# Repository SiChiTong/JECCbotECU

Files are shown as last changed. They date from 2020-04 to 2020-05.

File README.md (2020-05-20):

# JECCbotECU

See Istrobot 2020 demo video of JECCbot mini with JECCbotECU solving task of RoboOrienteering (https://robotika.vosrk.cz/roboorienteering/index.php?year=2020&page=aktuality ): https://www.youtube.com/watch?v=Fceis1Gl848 .

This Repository contains everything about controlling the JECCbot mini ( https://github.com/generationmake/JECCbot_mini ) with a the JECCbotECU board. There is also included software with web frontend for a Raspberry Pi, to move the robot to GPS waypoints.

## Hardware

### PCB

The JECCbotECU is formed from the controller board ( data included in this repository ) and some motor driver stage ( tested with https://github.com/generationmake/HighPowerMotorFeatherWing/ ). The controller pcb in this repository features a Bosch BNO055 IMU, the connection of a KVH C100 compass unit, GPS and RPLidar, USB VCOMM, different voltage regulators, GPIO port and SW-Debugging.

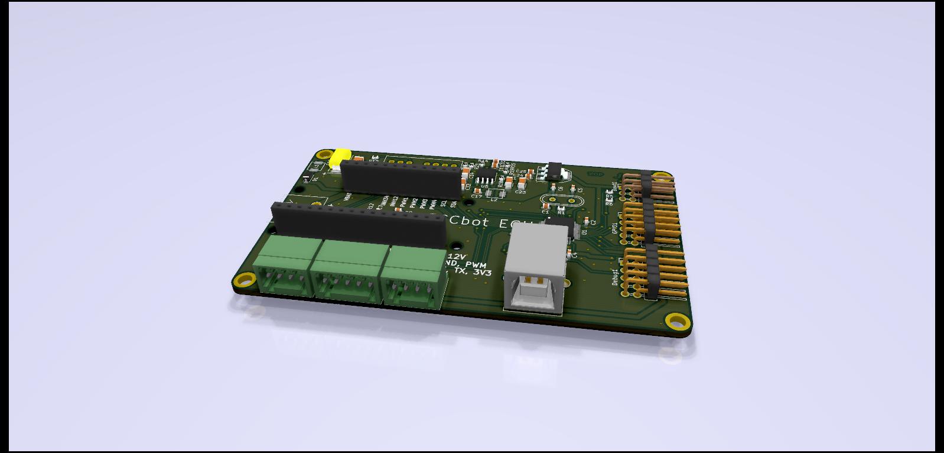
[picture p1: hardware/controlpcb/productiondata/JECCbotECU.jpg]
JECCbotECU rendering


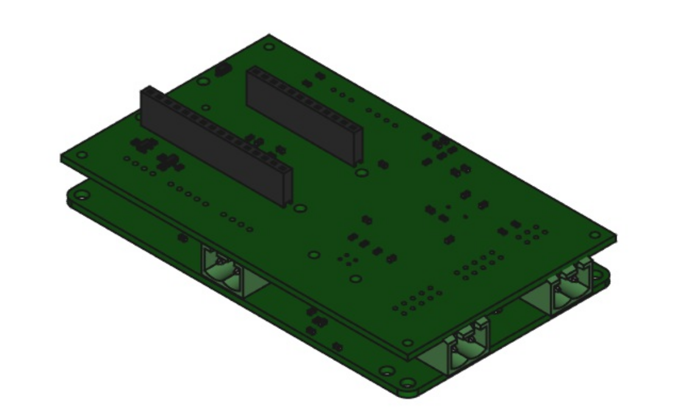
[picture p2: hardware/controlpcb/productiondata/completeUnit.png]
JECCbotECU with HighpowerMotorFeatherwing


### Case

There is also a case for the ECU unit with HighpowerMotorFeatherwing in this repository. It's size is 12cm x 10cm and it is fully compatible with the mountingholes on the JECCbot mini. On the top of the case, there is a snap in holder for a Einhell PowerXChange 18V drill battery.

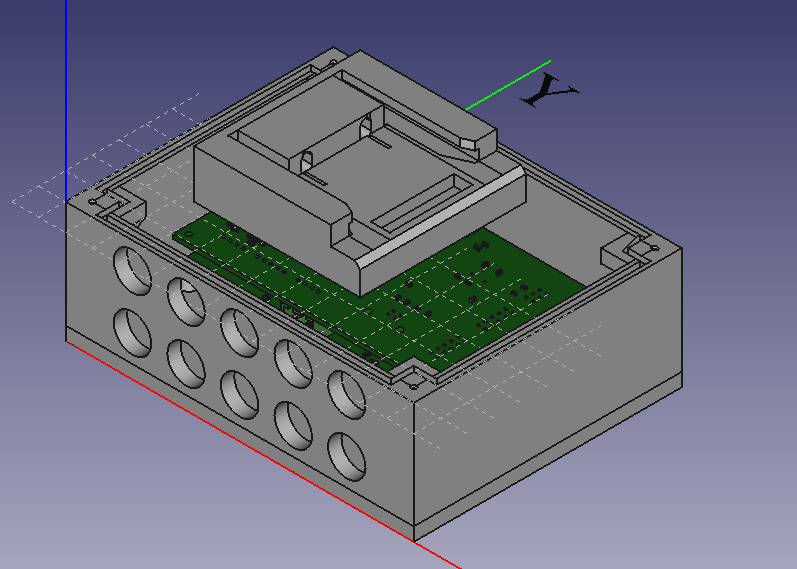
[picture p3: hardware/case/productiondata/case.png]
JECCbotECU case


## Software

### ECU 
 
The ECU Software is written in C using the STM32 Cube HAL hardware abstraction layer. It currently features control of two dc motors, emergency stop, rplidar, gps and compass decoding and driving the robot along a heading to north.

Here You can see the configured pinout of the STM32F103C8T6 mikrocontroller, which is compatible to STM32 Bluepill evalboard:

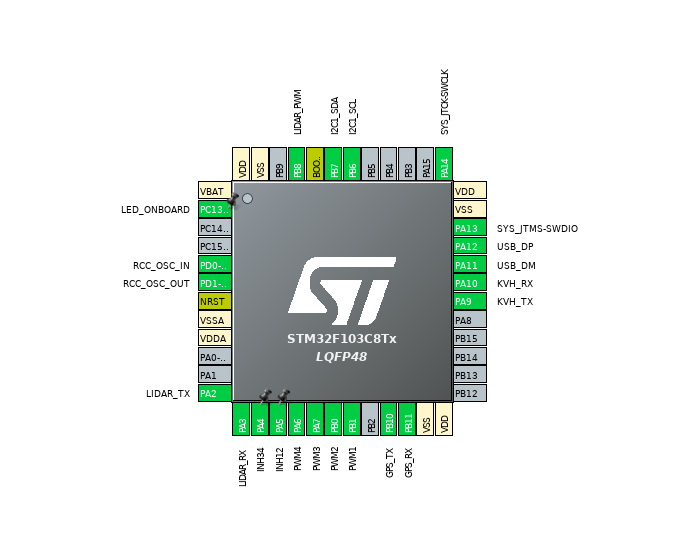
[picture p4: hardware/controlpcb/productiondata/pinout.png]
JECCbotECU pinout


#### Computer interaction

The ECU can interact with computer by using USB and a state based api.

##### Description of implemented states

###### State 0 - Joydrive

The direction and speed of the motors can be manipulated with the registers ```PWM_LEFT``` and ```PWM_RIGHT```. The value ranges are int16.

###### State 1 - Drive along compass heading

The robot can drive along a heading from -180° to 180° saved in the ```MOVEHEADING_HEADING``` register with a int16 speed in ```MOVEHEADING_SPEED``` by using a P-Controller with the parameter register ```MOVEHEADING_P```.

#### Protocol

The protocol is leaned on ASCII-Modbus and is register based. 

Every protocol instruction message begins with ```:```, which is followed with a 8 bit instructor. Then there is a 16 bit hex register address and a 16 bit or 32 bit hex register value ( interpreted as signed int ). Every message ends with ```\n```: 

```:<instructor><hex address><hex value>\n```

The mikrocontroller answers with ```:```, the register, value and ```\n```;

###### Protocol Configuration

```
API_MEMORY_SIZE 400

API_STATE_JOYDRIVE 0x0000
API_STATE_MOVEHEADING 0x0001

API_INSTRUCTION_READ 0x02
API_INSTRUCTION_WRITE 0x04

API_ERROR_WRONG_FORMAT 0x0000
API_ERROR_INVALID_ADDRESS 0x0001
API_ERROR_WRONG_INSTRUCTOR 0x0002
API_ERROR_ACCESS_DENIED 0x0003

API_REG_STATE 0x0000

API_REG_PWMLEFT 0x0002
API_REG_PWMRIGHT 0x0004

API_REG_MOVEHEADING_P 0x0005
API_REG_MOVEHEADING_SPEED 0x0006
API_REG_MOVEHEADING_HEADING 0x0007

API_BENCH_LIDAR_START 0x000f
API_BENCH_LIDAR_END API_BENCH_LIDAR_START + 360

API_REG_HEADING_KVH 0x0178

API_BENCH_GPS_START 0x0179
API_BENCH_GPS_END API_BENCH_GPS_START + 5
```

###### Example

Set robot state to 1:

Instruction: ```:04000000001\n``` -> Response ```:00000001\n```.

###### Error Codes

Every error code starts with the command e and has a specific index ( %03d ) as parameter, e. g. ```:e001\n```.

| Index | Meaning |
| ----- | ------- |
| 000 | received data is no command |
| 001 | Command is not found |
| 002 | Syntax error in command |

#### KVH Terminal

There is also a program included that lets the ECU act as a terminal to a connected KVH C100 compass unit. This can be used for calibrating the compass.

### Raspberry Pi

The main sotware used in the demonstration for Istrobot 2020 ( https://www.youtube.com/watch?v=Fceis1Gl848 ) is also included as a Codeblocks project.
In the html folder You can find the frontend design with commands to the robot via HTTP POST.

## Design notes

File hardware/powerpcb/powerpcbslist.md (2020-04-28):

# List of supported motor control / power pcbs

Generationmake HighpowermotorFeatherwing: https://github.com/generationmake/HighPowerMotorFeatherWing

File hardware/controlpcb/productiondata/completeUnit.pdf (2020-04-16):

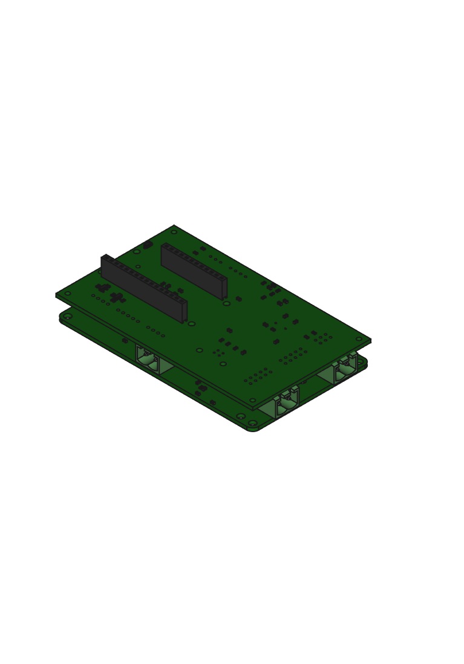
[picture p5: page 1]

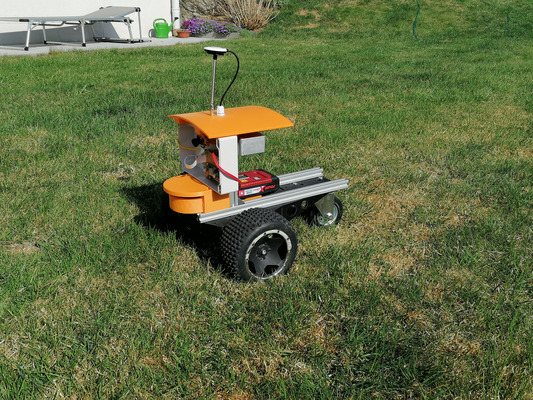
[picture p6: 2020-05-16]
software/html/titleImage.jpg

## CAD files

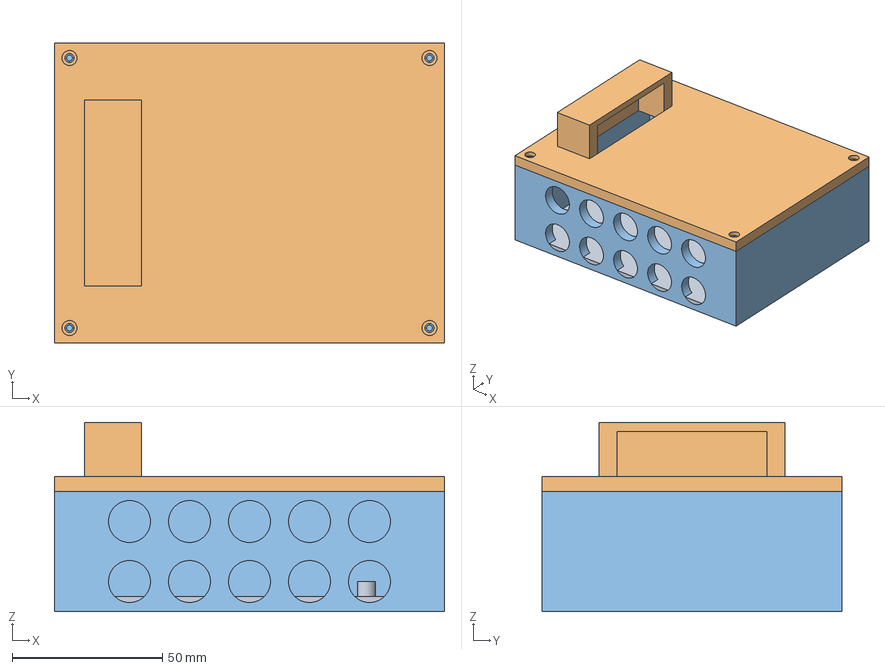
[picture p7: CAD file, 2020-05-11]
hardware/case/freecad/case.FCStd
130.0 x 100.0 x 63.0 mm
bottom
top
middle

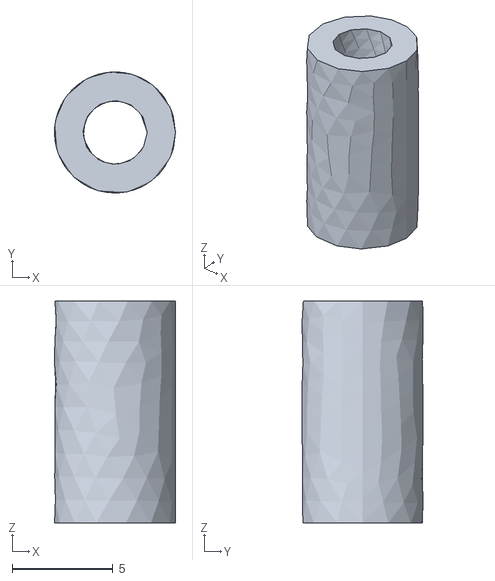
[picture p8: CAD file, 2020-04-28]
hardware/case/productiondata/spacer.stl
6.00 x 6.00 x 11.0

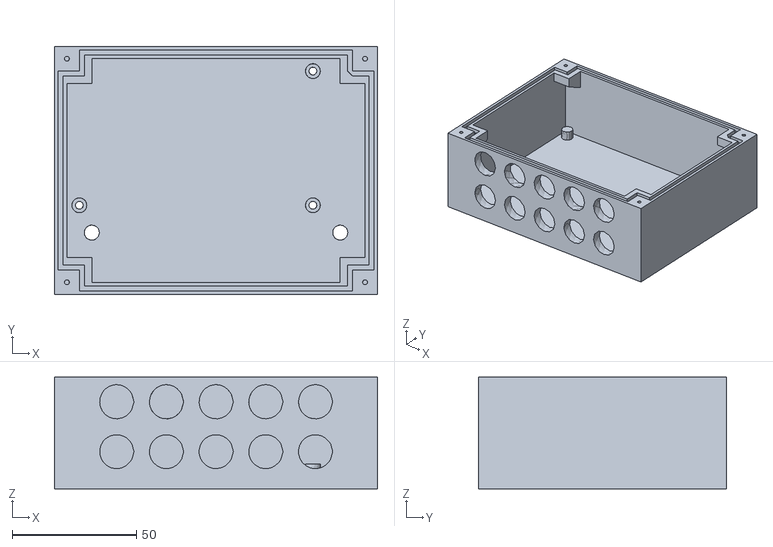
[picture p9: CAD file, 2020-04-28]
hardware/case/productiondata/lowercase.stl
130.0 x 100.0 x 45.0

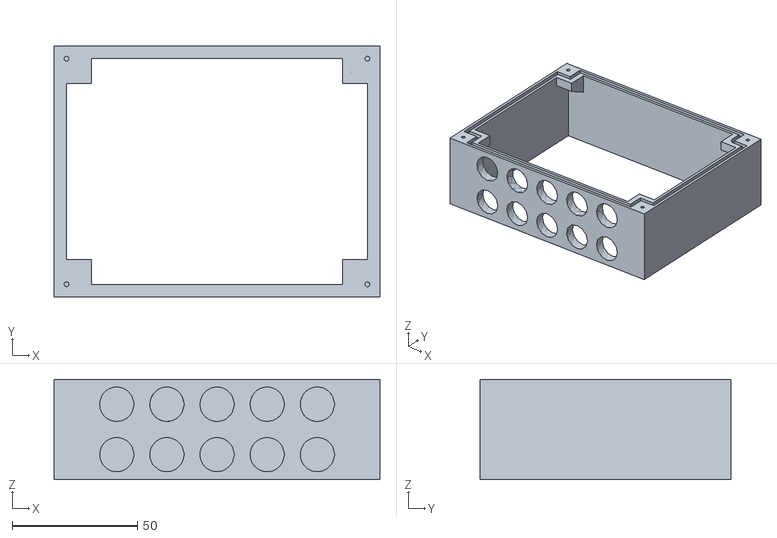
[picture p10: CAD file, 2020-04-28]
hardware/case/productiondata/middle.stl
130.0 x 100.0 x 40.0

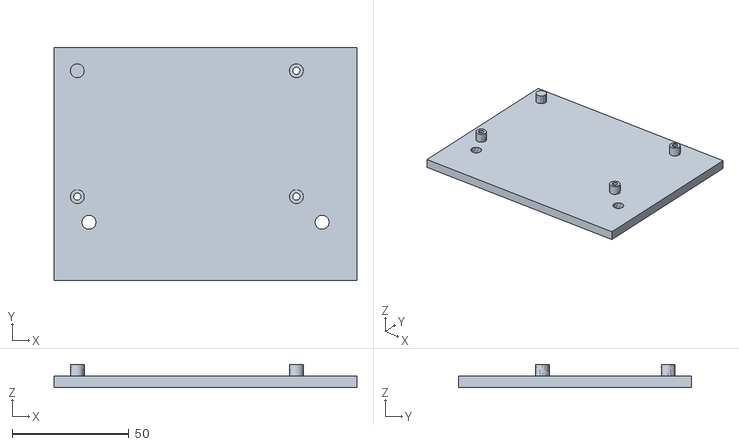
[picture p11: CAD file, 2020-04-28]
hardware/case/productiondata/bottom.stl
130.0 x 100.0 x 10.0

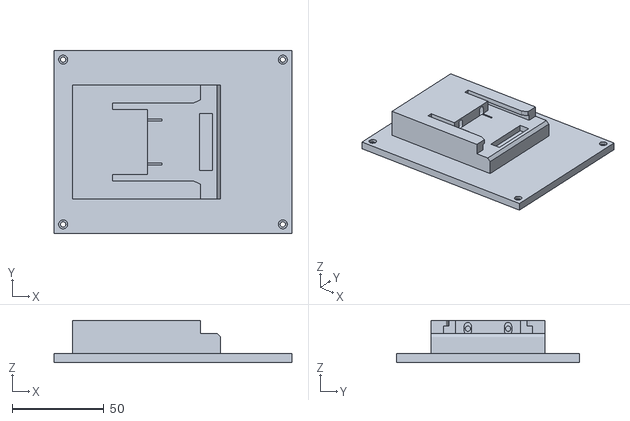
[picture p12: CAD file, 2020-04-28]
hardware/case/productiondata/uppercase.stl
130.0 x 100.0 x 23.0

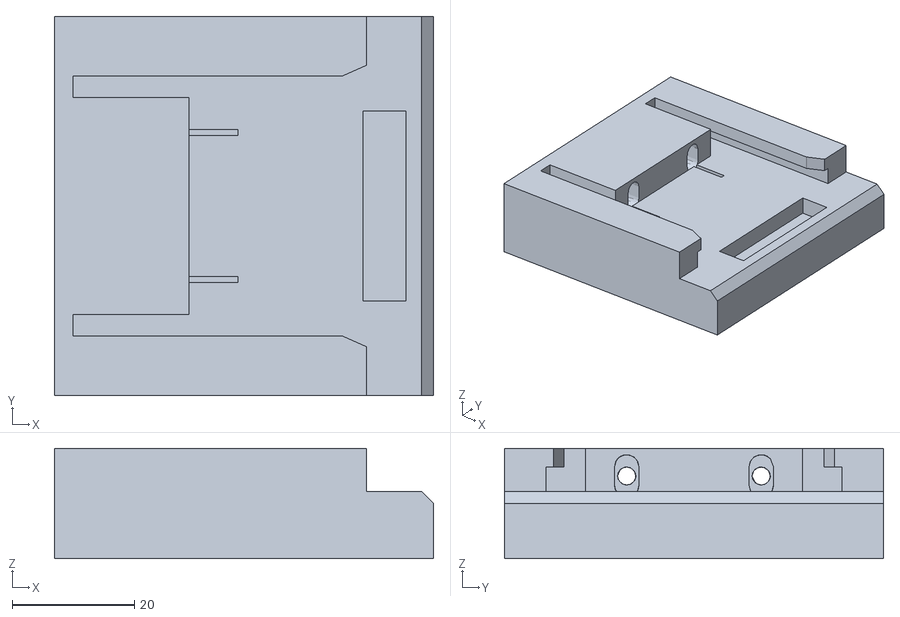
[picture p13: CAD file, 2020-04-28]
hardware/case/productiondata/batteryadapter.stl
62.0 x 62.0 x 18.0

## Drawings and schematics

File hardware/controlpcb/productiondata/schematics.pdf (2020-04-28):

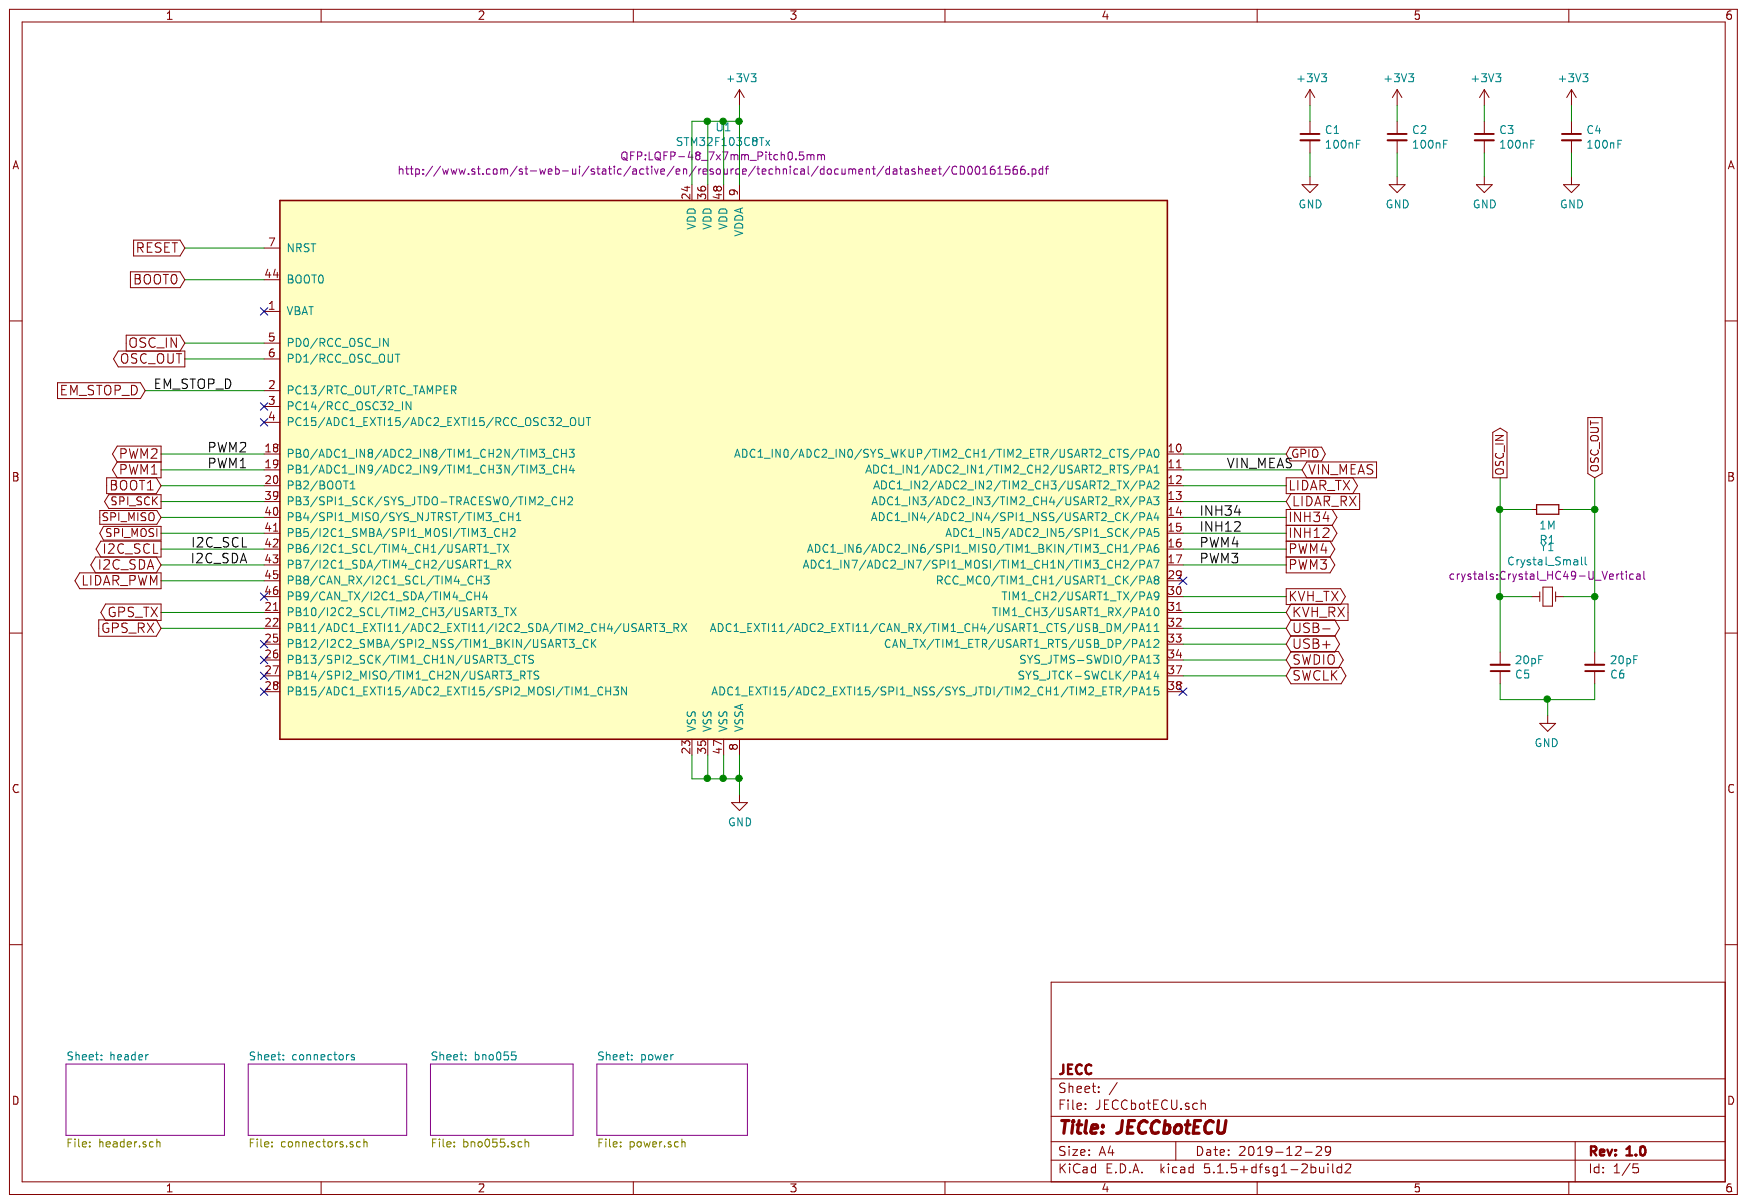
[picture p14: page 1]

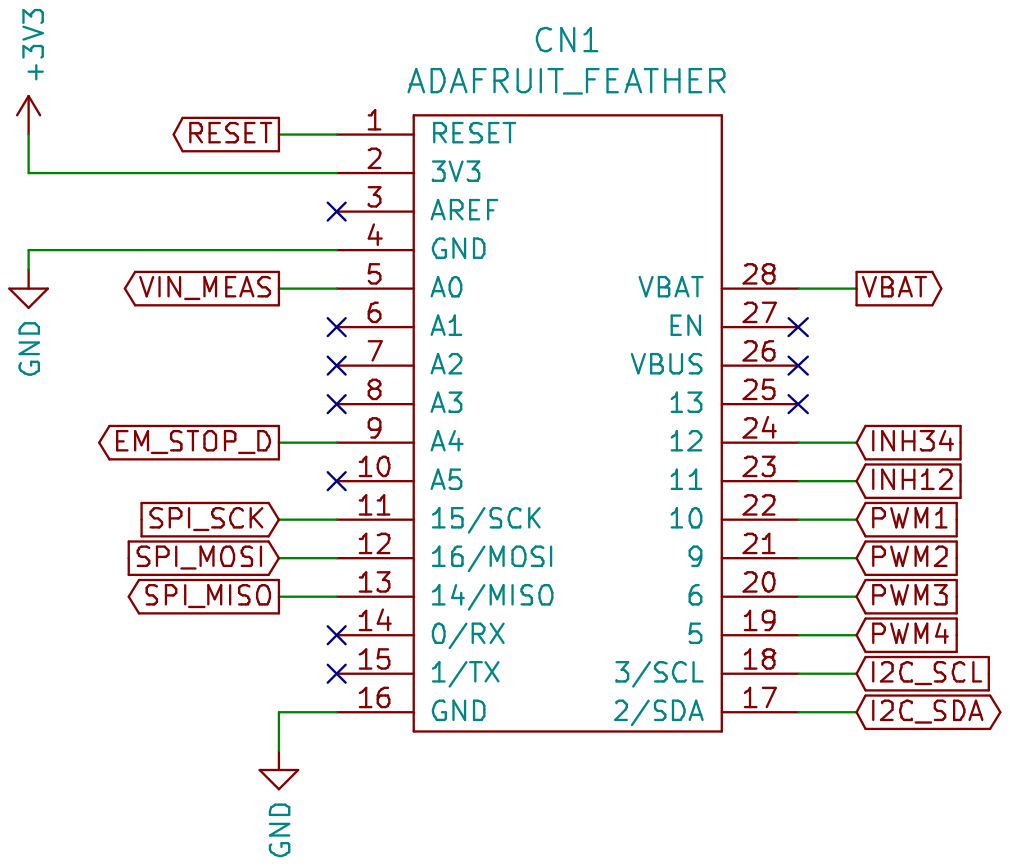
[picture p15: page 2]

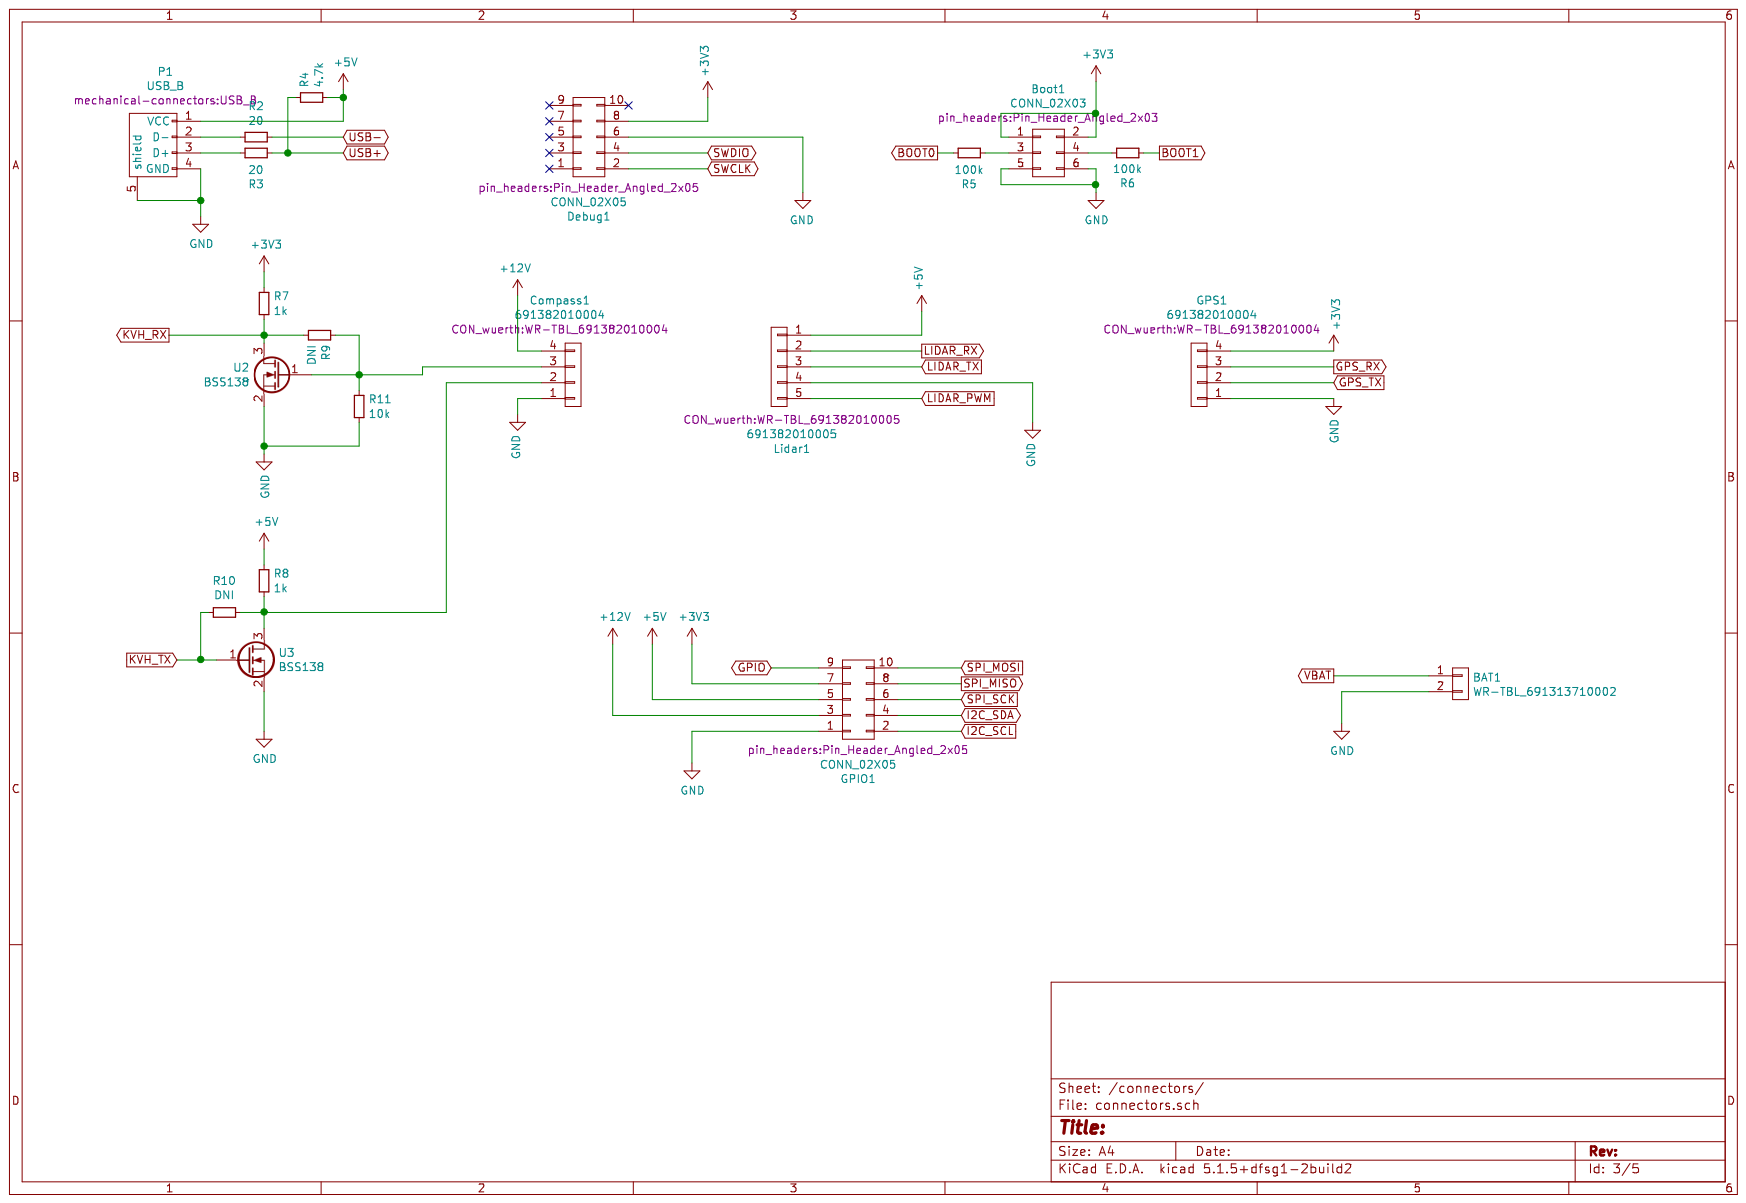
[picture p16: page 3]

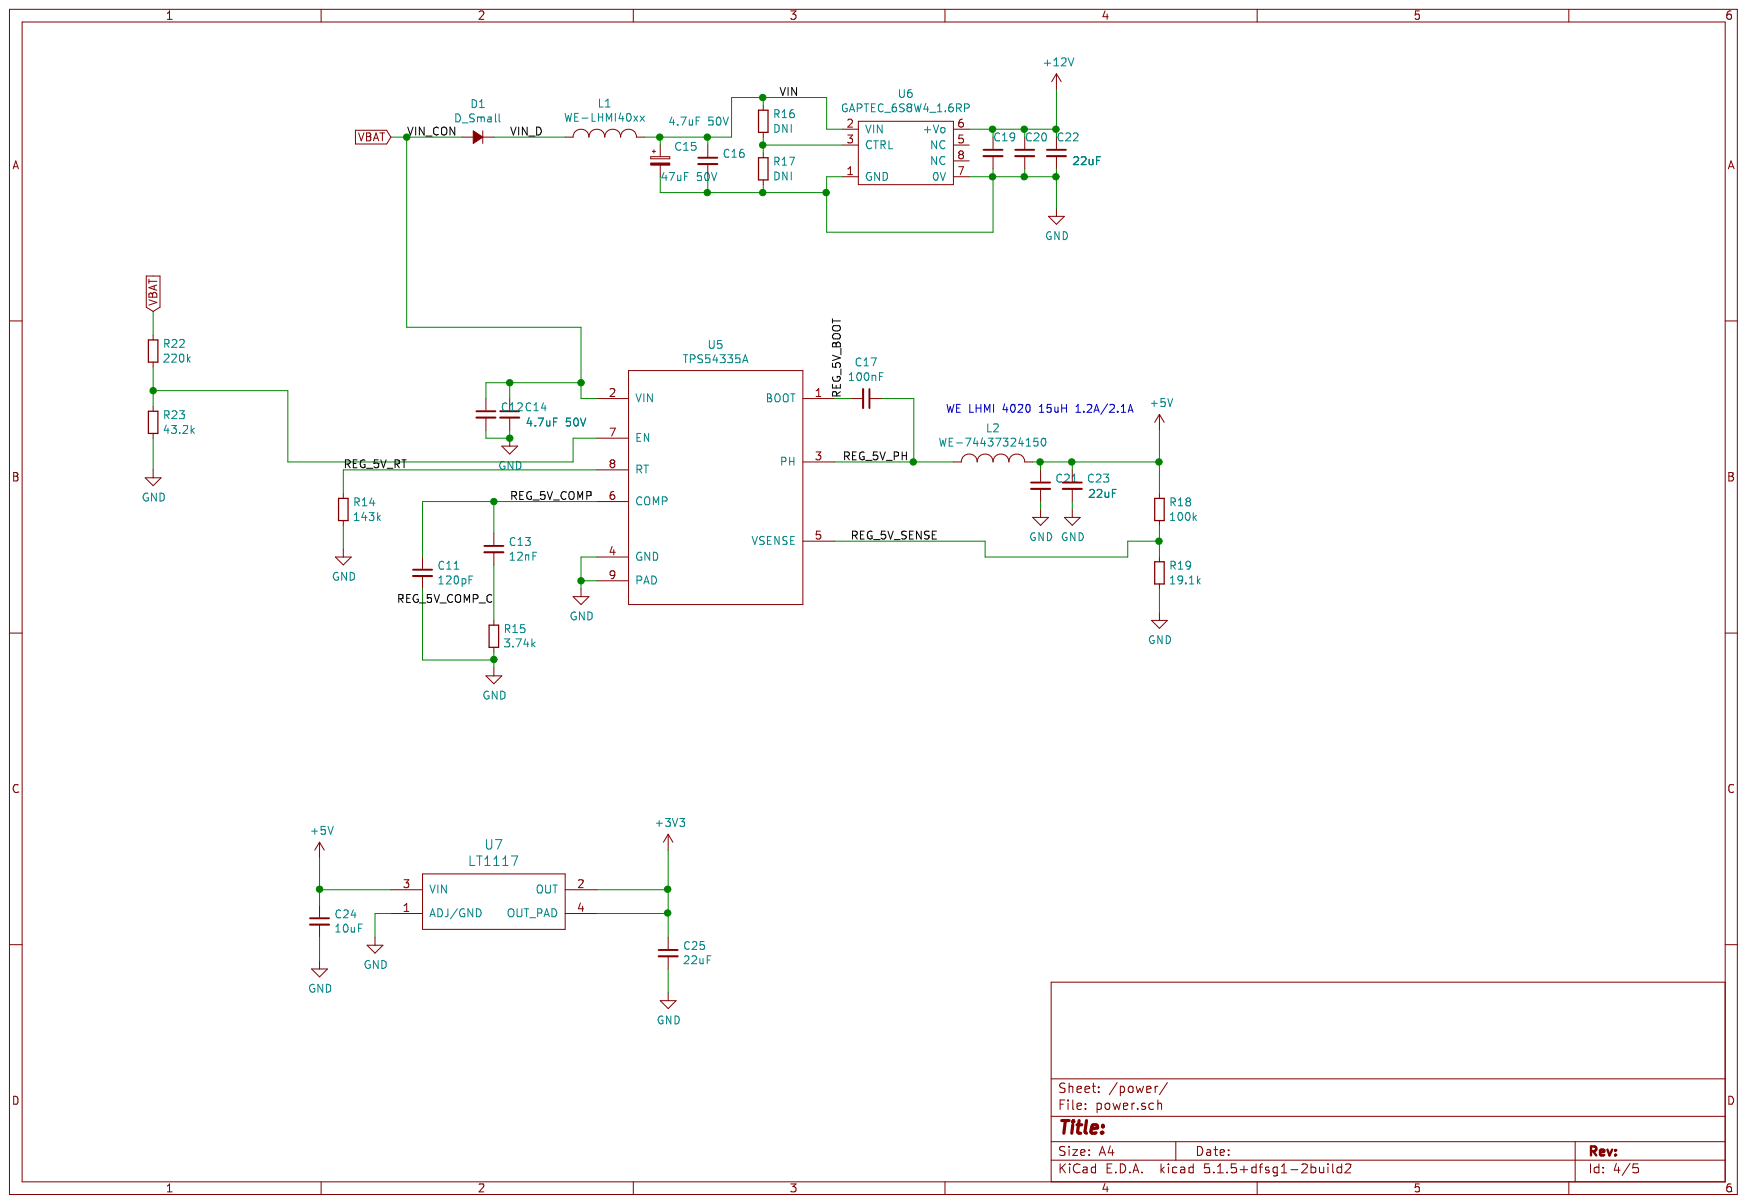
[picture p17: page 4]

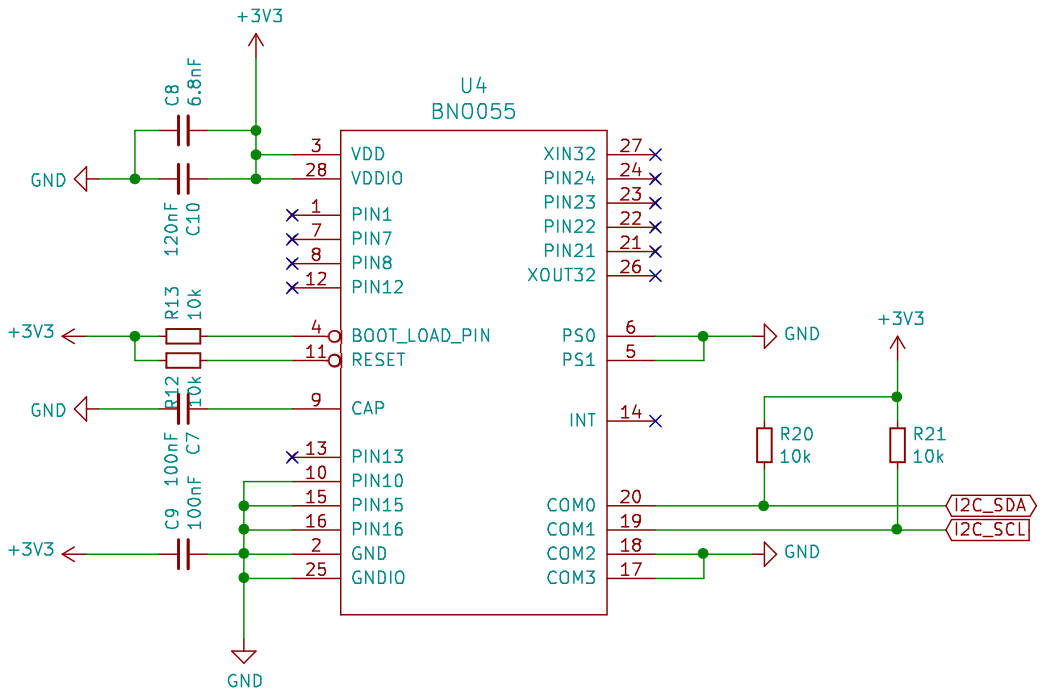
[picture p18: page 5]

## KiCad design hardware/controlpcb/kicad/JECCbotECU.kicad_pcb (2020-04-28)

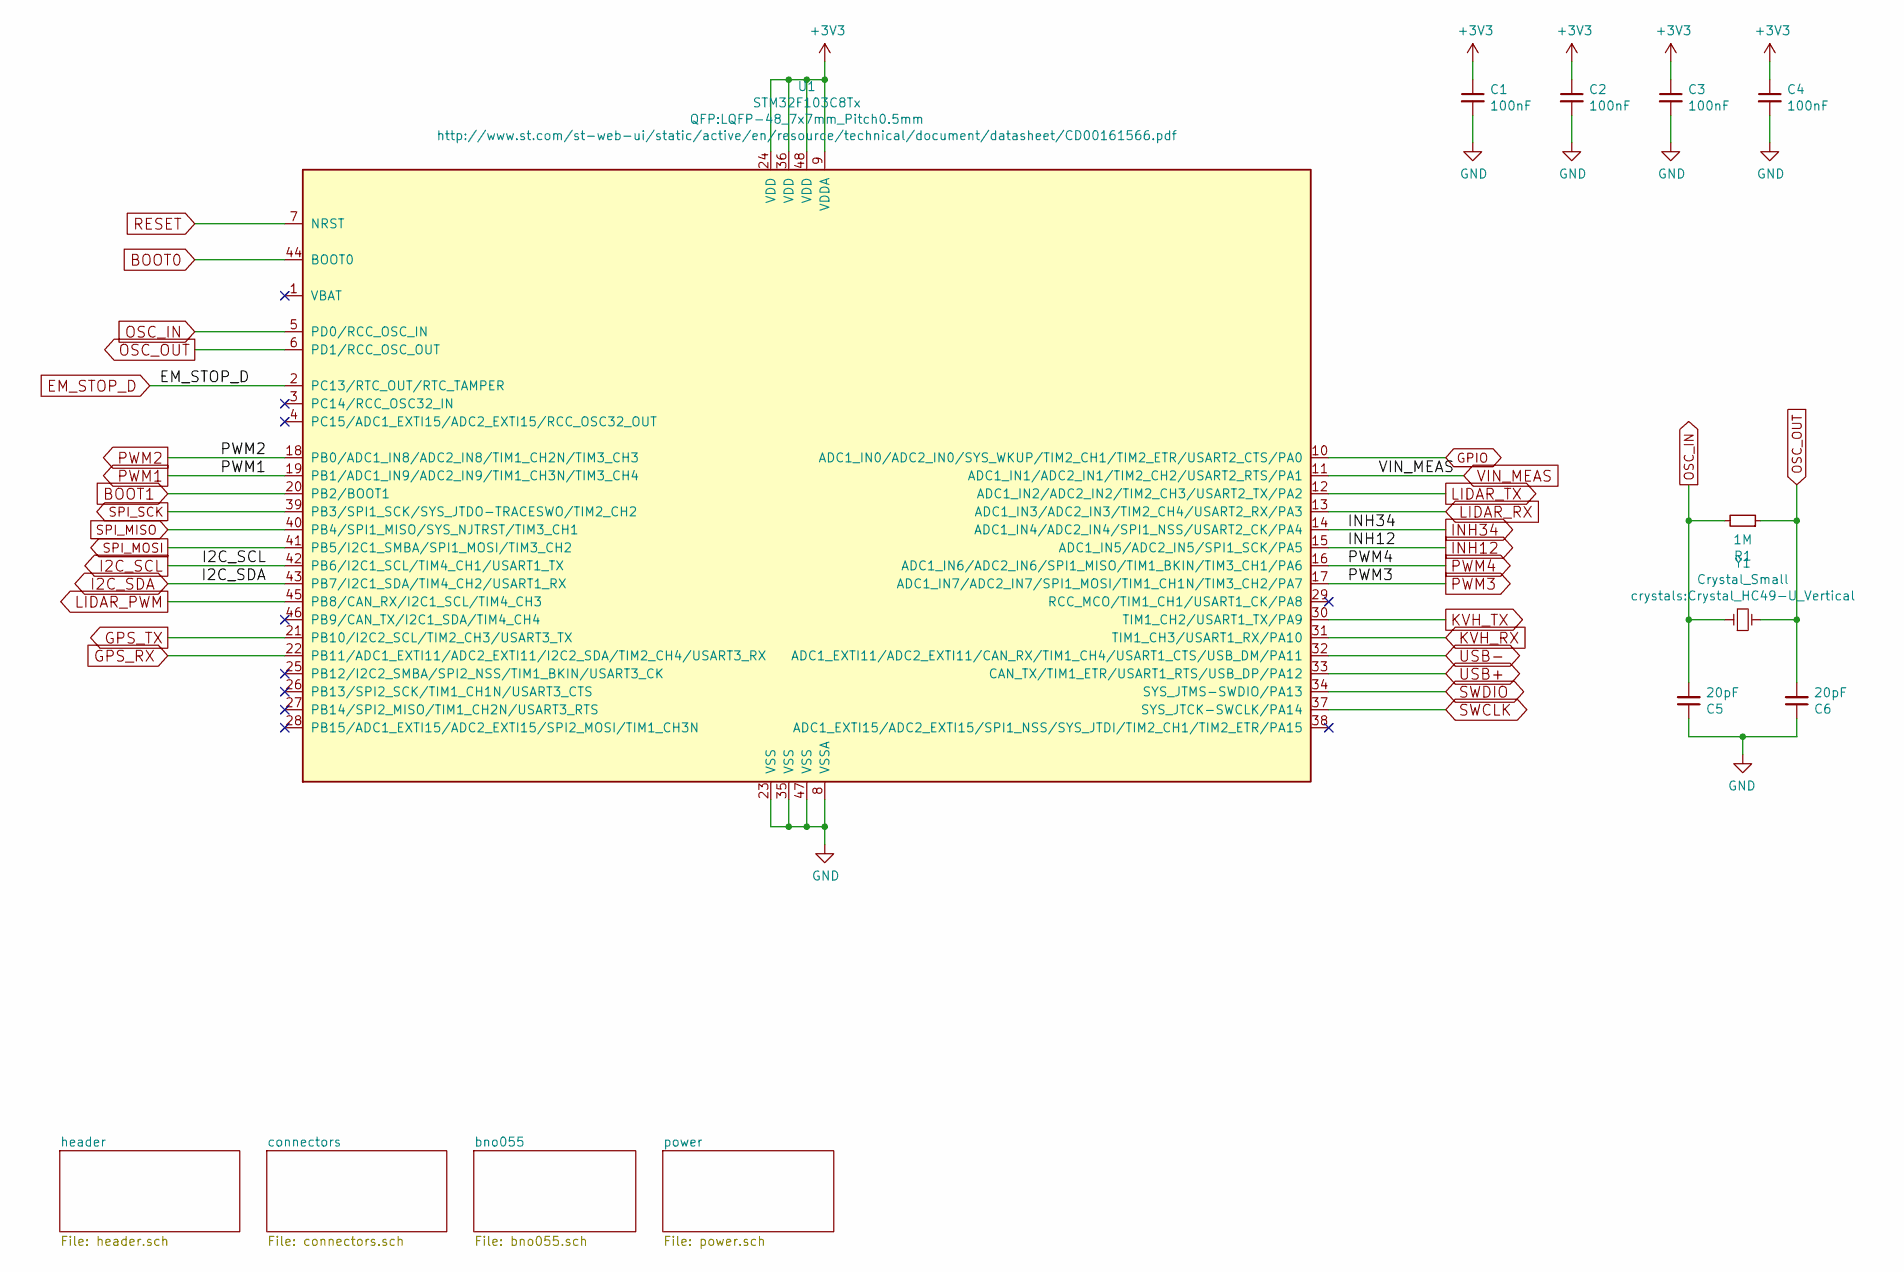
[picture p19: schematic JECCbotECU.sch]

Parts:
C1, C2, C3, C4: 100nF; C_0603
C5, C6: 20pF; C_0603
R1: 1M; R_0603
U1: STM32F103C8Tx; LQFP-48_7x7mm_Pitch0.5mm
Y1: Crystal_Small; Crystal_HC49-U_Vertical

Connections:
+3V3: C1.1, C2.1, C3.1, C4.1, U1.9 (VDDA), U1.24 (VDD), U1.36 (VDD), U1.48 (VDD); also elsewhere on the board
BOOT0: U1.44 (BOOT0); also elsewhere on the board
BOOT1: U1.20 (PB2/BOOT1); also elsewhere on the board
EM_STOP_D: U1.2 (PC13/RTC_OUT/RTC_TAMPER); also elsewhere on the board
GND: C1.2, C2.2, C3.2, C4.2, C5.1, C6.1, U1.8 (VSSA), U1.23 (VSS), U1.35 (VSS), U1.47 (VSS); also elsewhere on the board
GPIO: U1.10 (ADC1_IN0/ADC2_IN0/SYS_WKUP/TIM2_CH1/TIM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); also elsewhere on the board
GPS_RX: U1.22 (PB11/ADC1_EXTI11/ADC2_EXTI11/I2C2_SDA/T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); also elsewhere on the board
GPS_TX: U1.21 (PB10/I2C2_SCL/TIM2_CH3/USART3_TX); also elsewhere on the board
I2C_SCL: U1.42 (PB6/I2C1_SCL/TIM4_CH1/USART1_TX); also elsewhere on the board
I2C_SDA: U1.43 (PB7/I2C1_SDA/TIM4_CH2/USART1_RX); also elsewhere on the board
INH12: U1.15 (ADC1_IN5/ADC2_IN5/SPI1_SCK/PA5); also elsewhere on the board
INH34: U1.14 (ADC1_IN4/ADC2_IN4/SPI1_NSS/USART2_CK/PA4); also elsewhere on the board
KVH_RX: U1.31 (TIM1_CH3/USART1_RX/PA10); also elsewhere on the board
KVH_TX: U1.30 (TIM1_CH2/USART1_TX/PA9); also elsewhere on the board
LIDAR_PWM: U1.45 (PB8/CAN_RX/I2C1_SCL/TIM4_CH3); also elsewhere on the board
LIDAR_RX: U1.13 (ADC1_IN3/ADC2_IN3/TIM2_CH4/USART2_RX/PA3); also elsewhere on the board
LIDAR_TX: U1.12 (ADC1_IN2/ADC2_IN2/TIM2_CH3/USART2_TX/PA2); also elsewhere on the board
OSC_IN: C5.2, R1.2, U1.5 (PD0/RCC_OSC_IN), Y1.1
OSC_OUT: C6.2, R1.1, U1.6 (PD1/RCC_OSC_OUT), Y1.2
PWM1: U1.19 (PB1/ADC1_IN9/ADC2_IN9/TIM1_CH3N/TIM3_CH4); also elsewhere on the board
PWM2: U1.18 (PB0/ADC1_IN8/ADC2_IN8/TIM1_CH2N/TIM3_CH3); also elsewhere on the board
PWM3: U1.17 (ADC1_IN7/ADC2_IN7/SPI1_MOSI/TIM1_CH1N/T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); also elsewhere on the board
PWM4: U1.16 (ADC1_IN6/ADC2_IN6/SPI1_MISO/TIM1_BKIN/T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); also elsewhere on the board
RESET: U1.7 (NRST); also elsewhere on the board
SPI_MISO: U1.40 (PB4/SPI1_MISO/SYS_NJTRST/TIM3_CH1); also elsewhere on the board
SPI_MOSI: U1.41 (PB5/I2C1_SMBA/SPI1_MOSI/TIM3_CH2); also elsewhere on the board
SPI_SCK: U1.39 (PB3/SPI1_SCK/SYS_JTDO-TRACESWO/TIM2_CH2); also elsewhere on the board
SWCLK: U1.37 (SYS_JTCK-SWCLK/PA14); also elsewhere on the board
SWDIO: U1.34 (SYS_JTMS-SWDIO/PA13); also elsewhere on the board
USB+: U1.33 (CAN_TX/TIM1_ETR/USART1_RTS/USB_DP/PA12); also elsewhere on the board
USB-: U1.32 (ADC1_EXTI11/ADC2_EXTI11/CAN_RX/TIM1_CH4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); also elsewhere on the board
VIN_MEAS: U1.11 (ADC1_IN1/ADC2_IN1/TIM2_CH2/USART2_RTS/P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); also elsewhere on the board

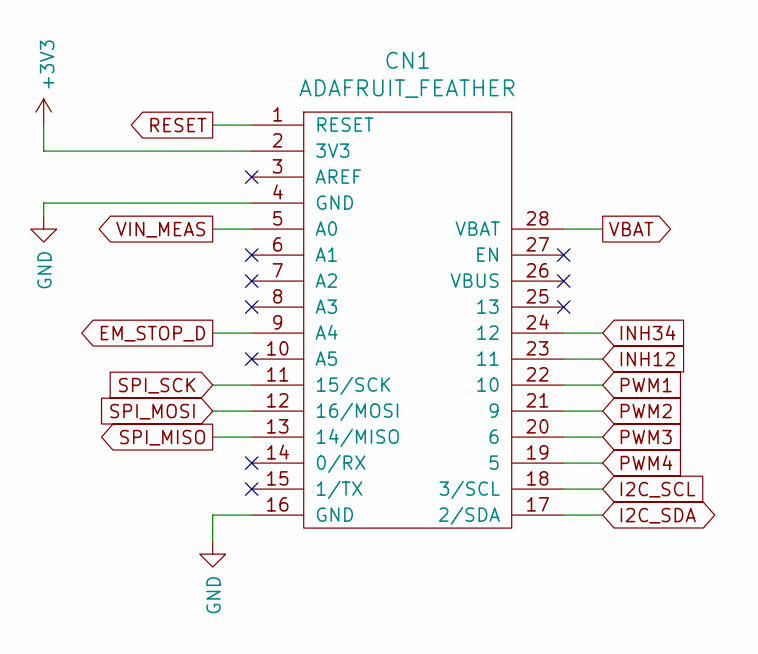
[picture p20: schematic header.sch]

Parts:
CN1: ADAFRUIT_FEATHER; ADAFRUIT_FEATHER_HOLES

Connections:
+3V3: CN1.2 (3V3); also elsewhere on the board
EM_STOP_D: CN1.9 (A4); also elsewhere on the board
GND: CN1.4 (GND), CN1.16 (GND); also elsewhere on the board
I2C_SCL: CN1.18 (3/SCL); also elsewhere on the board
I2C_SDA: CN1.17 (2/SDA); also elsewhere on the board
INH12: CN1.23 (11); also elsewhere on the board
INH34: CN1.24 (12); also elsewhere on the board
PWM1: CN1.22 (10); also elsewhere on the board
PWM2: CN1.21 (9); also elsewhere on the board
PWM3: CN1.20 (6); also elsewhere on the board
PWM4: CN1.19 (5); also elsewhere on the board
RESET: CN1.1 (RESET); also elsewhere on the board
SPI_MISO: CN1.13 (14/MISO); also elsewhere on the board
SPI_MOSI: CN1.12 (16/MOSI); also elsewhere on the board
SPI_SCK: CN1.11 (15/SCK); also elsewhere on the board
VBAT: CN1.28 (VBAT); also elsewhere on the board
VIN_MEAS: CN1.5 (A0); also elsewhere on the board

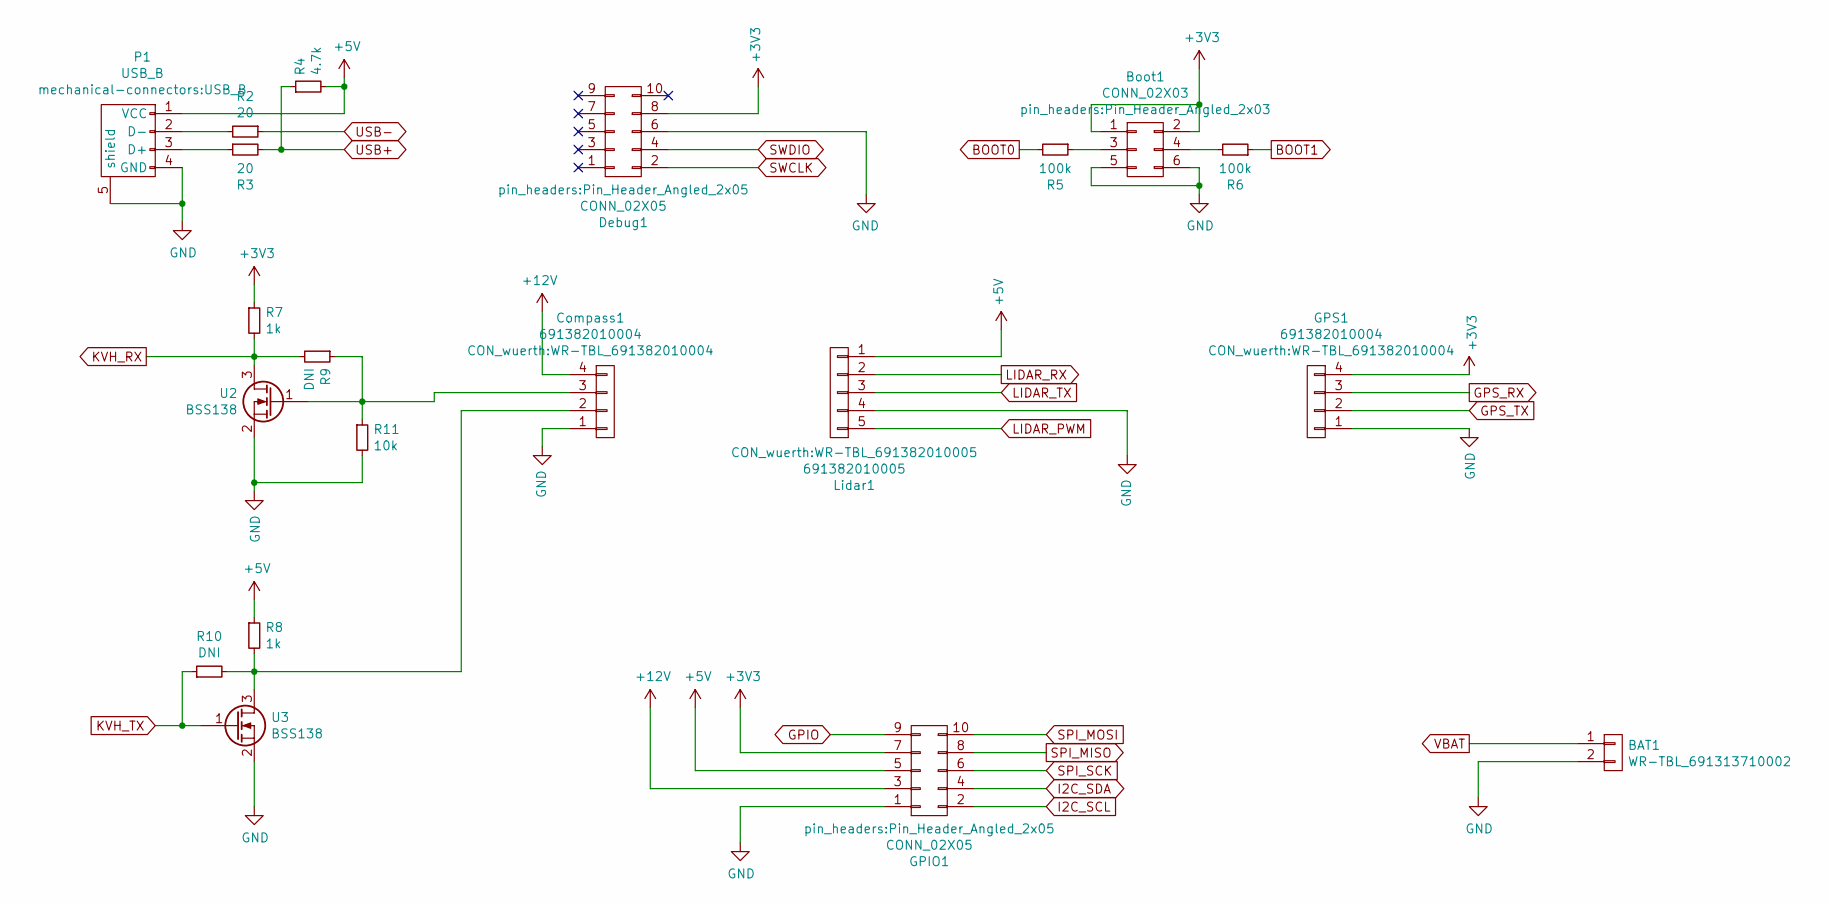
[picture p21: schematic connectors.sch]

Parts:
BAT1: WR-TBL_691313710002
Boot1: CONN_02X03; Pin_Header_Angled_2x03
Compass1: 691382010004; WR-TBL_691382010004
Debug1: CONN_02X05; Pin_Header_Angled_2x05
GPIO1: CONN_02X05; Pin_Header_Angled_2x05
GPS1: 691382010004; WR-TBL_691382010004
Lidar1: 691382010005; WR-TBL_691382010005
P1: USB_B
R2, R3: 20; R_0603
R4: 4.7k; R_0603
R5, R6: 100k; R_0603
R7, R8: 1k; R_0603
R9, R10: DNI; R_0603
R11: 10k; R_0603
U2, U3: BSS138; SOT-23

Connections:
+3V3: Boot1.1, Boot1.2, Debug1.8, GPIO1.7, GPS1.4, R7.1; also elsewhere on the board
+5V: GPIO1.5, Lidar1.1, P1.1 (VCC), R4.2, R8.1; also elsewhere on the board
+12V: Compass1.4, GPIO1.3; also elsewhere on the board
BOOT0: R5.2; also elsewhere on the board
BOOT1: R6.1; also elsewhere on the board
GND: BAT1.2, Boot1.5, Boot1.6, Compass1.1, Debug1.6, GPIO1.1, GPS1.1, Lidar1.4, P1.4 (GND), P1.5 (shield), R11.2, U2.2, U3.2; also elsewhere on the board
GPIO: GPIO1.9; also elsewhere on the board
GPS_RX: GPS1.3; also elsewhere on the board
GPS_TX: GPS1.2; also elsewhere on the board
I2C_SCL: GPIO1.2; also elsewhere on the board
I2C_SDA: GPIO1.4; also elsewhere on the board
KVH_RX: R7.2, R9.2, U2.3; also elsewhere on the board
KVH_TX: R10.1, U3.1; also elsewhere on the board
LIDAR_PWM: Lidar1.5; also elsewhere on the board
LIDAR_RX: Lidar1.2; also elsewhere on the board
LIDAR_TX: Lidar1.3; also elsewhere on the board
unnamed: Boot1.3, R5.1
unnamed: Boot1.4, R6.2
unnamed: Compass1.2, R8.2, R10.2, U3.3
unnamed: Compass1.3, R9.1, R11.1, U2.1
unnamed: P1.2 (D-), R2.2
unnamed: P1.3 (D+), R3.1
SPI_MISO: GPIO1.8; also elsewhere on the board
SPI_MOSI: GPIO1.10; also elsewhere on the board
SPI_SCK: GPIO1.6; also elsewhere on the board
SWCLK: Debug1.2; also elsewhere on the board
SWDIO: Debug1.4; also elsewhere on the board
USB+: R3.2, R4.1; also elsewhere on the board
USB-: R2.1; also elsewhere on the board
VBAT: BAT1.1; also elsewhere on the board

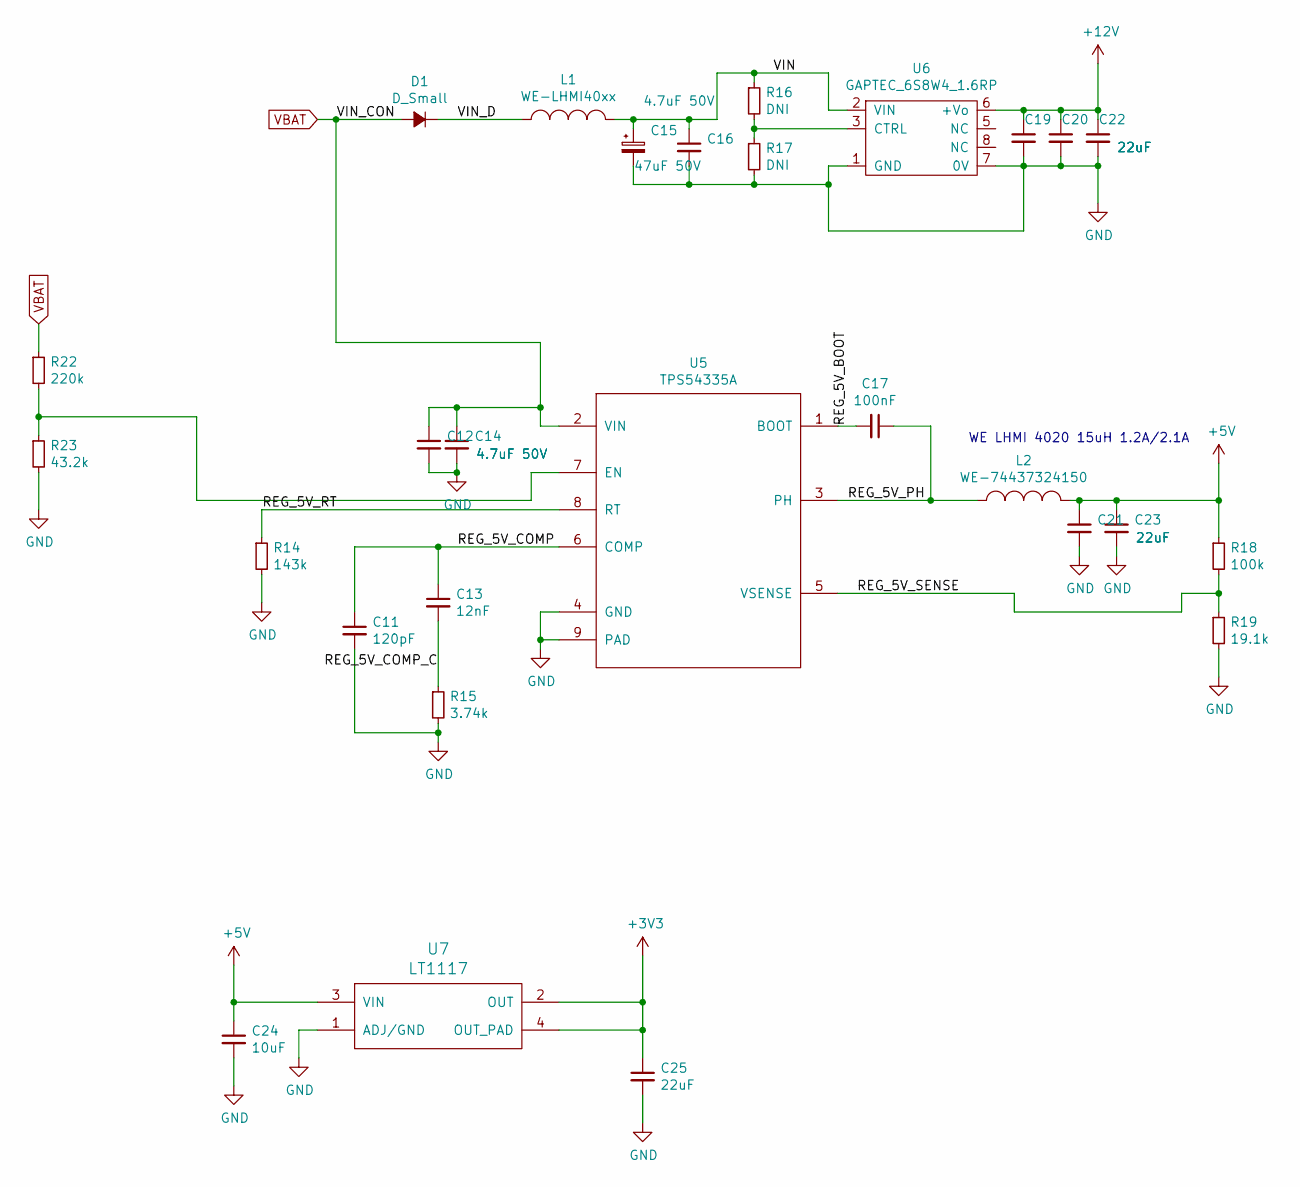
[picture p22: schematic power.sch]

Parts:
C11: 120pF; C_0603
C12, C14: 4.7uF 50V; C_1206
C13: 12nF; C_0603
C15: 47uF 50V; TantalC_SizeD_EIA-7343_Wave
C16: 4.7uF 50V; C_1210
C17: 100nF; C_0603
C19, C20, C21, C22, C23: 22uF; C_1206
C24: 10uF; C_0603
C25: 22uF; C_0603
D1: D_Small; SOD-123
L1: WE-LHMI40xx
L2: WE-74437324150; WE-LHMI40xx
R14: 143k; R_0603
R15: 3.74k; R_0603
R16, R17: DNI; R_0603
R18: 100k; R_0603
R19: 19.1k; R_0603
R22: 220k; R_0603
R23: 43.2k; R_0603
U5: TPS54335A; SOIC-8-1EP_3.9x4.9mm_Pitch1.27mm
U6: GAPTEC_6S8W4_1.6RP
U7: LT1117; SOT-223

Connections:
+3V3: C25.1, U7.2 (OUT), U7.4 (OUT_PAD); also elsewhere on the board
+5V: C21.1, C23.1, C24.1, L2.2, R18.1, U7.3 (VIN); also elsewhere on the board
+12V: C19.1, C20.1, C22.1, U6.6 (+Vo); also elsewhere on the board
/power/REG_5V_BOOT: C17.2, U5.1 (BOOT)
/power/REG_5V_COMP: C11.1, C13.1, U5.6 (COMP)
/power/REG_5V_COMP_C: C13.2, R15.1
/power/REG_5V_PH: C17.1, L2.1, U5.3 (PH)
/power/REG_5V_RT: R14.1, U5.8 (RT)
/power/REG_5V_SENSE: R18.2, R19.1, U5.5 (VSENSE)
/power/VIN: C15.1, C16.1, L1.2, R16.1, U6.2 (VIN)
/power/VIN_D: D1.1 (K), L1.1
GND: C11.2, C12.2, C14.2, C15.2, C16.2, C19.2, C20.2, C21.2, C22.2, C23.2, C24.2, C25.2, R14.2, R15.2, R17.2, R19.2, R23.2, U5.4 (GND), U5.9 (PAD), U6.1 (GND), U6.7 (0V), U7.1 (ADJ/GND); also elsewhere on the board
unnamed: R16.2, R17.1, U6.3 (CTRL)
unnamed: R22.2, R23.1, U5.7 (EN)
VBAT: C12.1, C14.1, D1.2 (A), R22.1, U5.2 (VIN); also elsewhere on the board

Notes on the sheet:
WE LHMI 4020 15uH 1.2A/2.1A

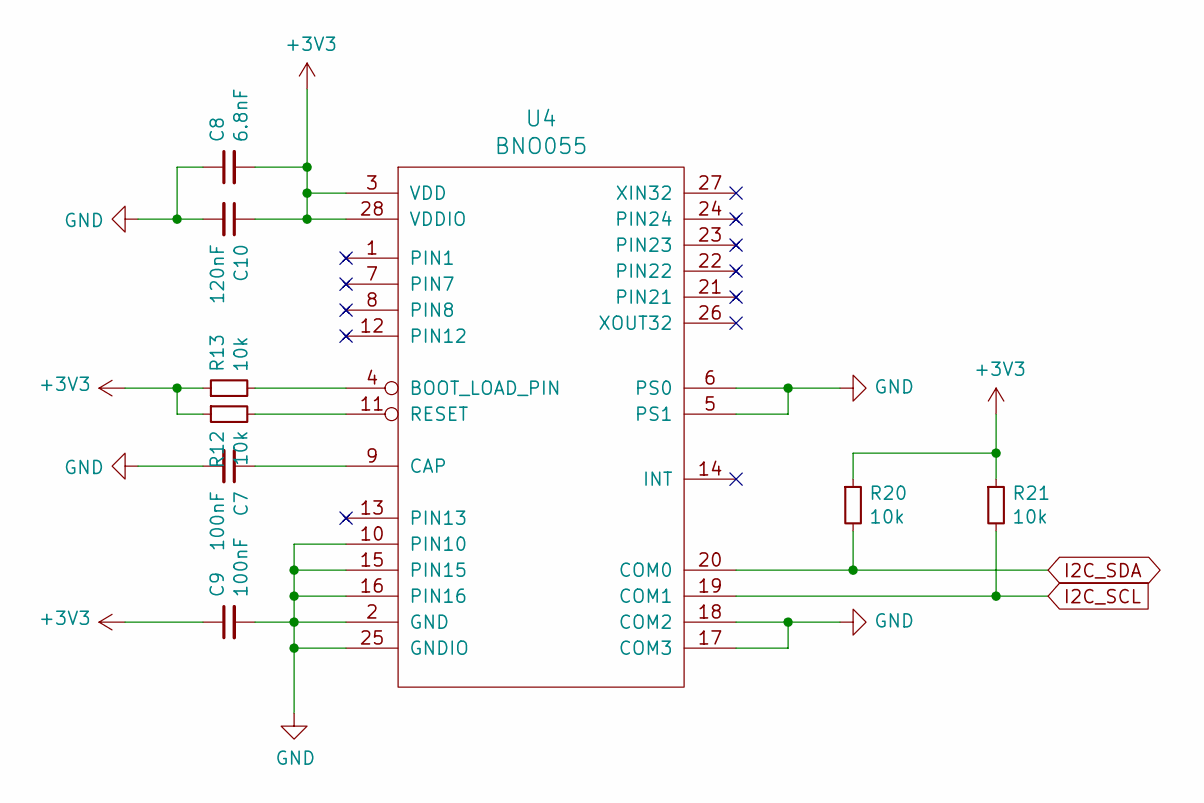
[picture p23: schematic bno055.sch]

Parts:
C7, C9: 100nF; C_0603
C8: 6.8nF; C_0603
C10: 120nF; C_0603
R12, R13, R20, R21: 10k; R_0603
U4: BNO055; LGA-28-5832

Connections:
+3V3: C8.2, C9.1, C10.1, R12.1, R13.1, R20.1, R21.1, U4.3 (VDD), U4.28 (VDDIO); also elsewhere on the board
GND: C7.2, C8.1, C9.2, C10.2, U4.2 (GND), U4.5 (PS1), U4.6 (PS0), U4.10 (PIN10), U4.15 (PIN15), U4.16 (PIN16), U4.17 (COM3), U4.18 (COM2), U4.25 (GNDIO); also elsewhere on the board
I2C_SCL: R21.2, U4.19 (COM1); also elsewhere on the board
I2C_SDA: R20.2, U4.20 (COM0); also elsewhere on the board
unnamed: C7.1, U4.9 (CAP)
unnamed: R12.2, U4.11 (RESET)
unnamed: R13.2, U4.4 (BOOT_LOAD_PIN)

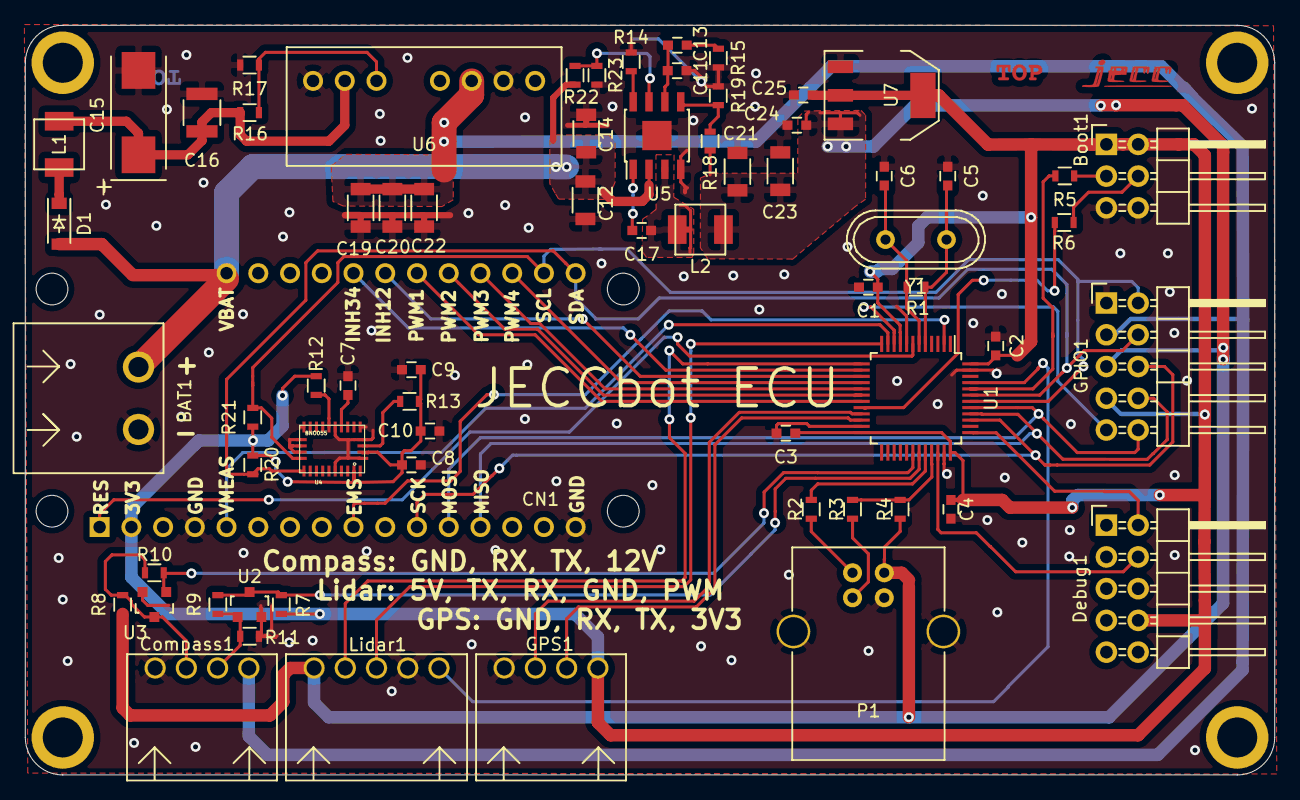
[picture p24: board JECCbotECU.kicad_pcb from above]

Board: 2 copper layers, 100.0 x 60.0 mm, 71 parts (0 on the bottom side), 54 nets.

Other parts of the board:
MH1, MH2, MH3, MH4: MHP_3.2_5.0

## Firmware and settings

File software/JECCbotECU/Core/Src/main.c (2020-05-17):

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

/* Includes ------------------------------------------------------------------*/
#include "main.h"
#include "usb_device.h"

/* USER CODE BEGIN PD */
#define LIDAR_STATE_INIT 0
#define LIDAR_STATE_SCAN 1
/* USER CODE END PD */

I2C_HandleTypeDef hi2c1;

TIM_HandleTypeDef htim3;
TIM_HandleTypeDef htim4;

UART_HandleTypeDef huart1;
UART_HandleTypeDef huart2;
UART_HandleTypeDef huart3;

/* USER CODE BEGIN PV */
NmeaString kvhString;
NmeaString gpsString;

/* USER CODE END PV */

void SystemClock_Config(void);
static void MX_GPIO_Init(void);
static void MX_USART2_UART_Init(void);
static void MX_I2C1_Init(void);
static void MX_TIM3_Init(void);
static void MX_TIM4_Init(void);
static void MX_USART1_UART_Init(void);
static void MX_USART3_UART_Init(void);
/* USER CODE BEGIN PFP */
void powertrainInit();

void powertrainEnableMotors(int enableState);

void powertrainSetSpeeds(int16_t left, int16_t right);

void kvhInit();
void kvhFetch();
void kvhDecode();

void gpsInit();
void gpsFetch();
void gpsDecode();

void insertSensordataToApi();
/* USER CODE END PFP */

/* USER CODE BEGIN 0 */
void HAL_UART_RxCpltCallback(UART_HandleTypeDef *huart)
{
	if(huart->Instance == huart1.Instance)
	{
		kvhFetch();
	}
	else if(huart->Instance == huart2.Instance)
	{
		//lidarDecode();
	}
	else if(huart->Instance == huart3.Instance)
	{
		gpsFetch();
	}
}
/* USER CODE END 0 */

/**
  * @brief  The application entry point.
  * @retval int
  */
int main(void)
{
  /* MCU Configuration--------------------------------------------------------*/

  /* Reset of all peripherals, Initializes the Flash interface and the Systick. */
  HAL_Init();

  /* Configure the system clock */
  SystemClock_Config();

  /* Initialize all configured peripherals */
  MX_GPIO_Init();
  MX_USB_DEVICE_Init();
  MX_USART2_UART_Init();
  MX_I2C1_Init();
  MX_TIM3_Init();
  MX_TIM4_Init();
  MX_USART1_UART_Init();
  MX_USART3_UART_Init();
  /* USER CODE BEGIN 2 */
  apiInit();

  powertrainInit();

  kvhInit();

  gpsInit();



  /* USER CODE END 2 */

  /* Infinite loop */
  /* USER CODE BEGIN WHILE */
  while (1)
  {
	  ApiInstruction ins = apiUpdate();

	  insertSensordataToApi();

	  if(ins.responseLen > 0)
	  {
		  CDC_Transmit_FS(ins.response, ins.responseLen);
	  }

	  if(API_STATE_JOYDRIVE == apiMemory[API_REG_STATE])
	  {
		  powertrainSetSpeeds(apiMemory[API_REG_PWMLEFT], apiMemory[API_REG_PWMRIGHT]);
	  }
	  else if(API_STATE_MOVEHEADING == apiMemory[API_REG_STATE])
	  {
		  moveHeading();
		  powertrainSetSpeeds(apiMemory[API_REG_PWMLEFT], apiMemory[API_REG_PWMRIGHT]);
	  }
//	  else if(API_STATE_MOVEGPS == apiMemory[API_REG_STATE])
//	  {
//		  moveGPS();
//		  powertrainSetSpeeds(apiMemory[API_REG_PWMLEFT], apiMemory[API_REG_PWMRIGHT]);
//	  }

    /* USER CODE END WHILE */

    /* USER CODE BEGIN 3 */
  }
  /* USER CODE END 3 */
}

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
/* USER CODE BEGIN 4 */
void powertrainInit()
{
	HAL_TIM_PWM_Start(&htim3, TIM_CHANNEL_1);
    HAL_TIM_PWM_Start(&htim3, TIM_CHANNEL_2);
	HAL_TIM_PWM_Start(&htim3, TIM_CHANNEL_3);
	HAL_TIM_PWM_Start(&htim3, TIM_CHANNEL_4);

	powertrainEnableMotors(1);

	powertrainSetSpeeds(0, 0);
}


void powertrainEnableMotors(int enableState)
{
	HAL_GPIO_WritePin(INH12_GPIO_Port, INH12_Pin, enableState);
	HAL_GPIO_WritePin(INH34_GPIO_Port, INH34_Pin, enableState);
}

void powertrainSetSpeeds(int16_t left, int16_t right)
{
	if(left < 0)
	{
		left = -left;
		htim3.Instance->CCR3 = 0;
		htim3.Instance->CCR4 = left;
	}
	else
	{
		htim3.Instance->CCR3 = left;
		htim3.Instance->CCR4 = 0;
	}

	if(right < 0)
	{
		right = -right;
		htim3.Instance->CCR1 = 0;
		htim3.Instance->CCR2 = right;
	}
	else
	{
		htim3.Instance->CCR1 = right;
		htim3.Instance->CCR2 = 0;
	}
}

void kvhInit()
{
	  char kvhInitStr[3] = { 's', '\r' };
	  char kvhConfigNmeaStr[5] = { '=', 't' , ',', '0', '\r' };
	  char kvhConfigSpeedStr[7] = { '=', 'r', ',' , '6', '0', '0', '\r' };
	  char kvhConfigUnitStr[5] = { '=', 'i' , ',', 'd', '\r' };
	  HAL_UART_Transmit(&huart1, kvhInitStr, 2, 1000);
	  HAL_Delay(100);
	  HAL_UART_Transmit(&huart1, kvhConfigNmeaStr, 5, 1000);
	  HAL_Delay(100);
	  HAL_UART_Transmit(&huart1, kvhConfigUnitStr, 5, 1000);
	  HAL_Delay(100);
	  HAL_UART_Transmit(&huart1, kvhConfigSpeedStr, 7, 1000);

	  kvhString.available = false;

	  HAL_UART_Receive_IT(&huart1, kvhString.nmeaStr, 1);
}

void kvhFetch()
{
	static bool startFound = false;

	if('$' == kvhString.nmeaStr[0])
	{
		if(startFound)
		{
			startFound = false;
			kvhString.available = true;
		}
		else
		{
			startFound = true;
			HAL_UART_Receive_IT(&huart1, &kvhString.nmeaStr[1], NMEA_STR_LEN - 2);
		}
	}
	else
	{
		startFound = false;
		HAL_UART_Receive_IT(&huart1, kvhString.nmeaStr, 1);
	}
}

void kvhDecode()
{
	if(kvhString.available)
	{
		kvhString.available = false;
		kvhString.nmeaStr[NMEA_HCHDT_LEN] = '\0';
		nmeaDecodeToApi(&kvhString);
		HAL_UART_Receive_IT(&huart1, kvhString.nmeaStr, 1);
	}
}

void gpsInit()
{
		gpsString.available = false;
		HAL_UART_Receive_IT(&huart3, gpsString.nmeaStr, 1);
}

void gpsFetch()
{
	static bool startFound = false;

	if('$' == gpsString.nmeaStr[0])
	{
		if(startFound)
		{
			startFound = false;
			gpsString.available = true;
		}
		else
		{
			startFound = true;
			HAL_UART_Receive_IT(&huart3, &gpsString.nmeaStr[1], NMEA_STR_LEN - 2);
		}
	}
	else
	{
		startFound = false;
		HAL_UART_Receive_IT(&huart3, gpsString.nmeaStr, 1);
	}
}

void gpsDecode()
{
	if(gpsString.available)
	{
		gpsString.available = false;
		gpsString.nmeaStr[NMEA_GPRMC_LEN] = '\0';
		nmeaDecodeToApi(&gpsString);
		HAL_UART_Receive_IT(&huart3, gpsString.nmeaStr, 1);
	}
}

void insertSensordataToApi()
{
	kvhDecode();
	gpsDecode();
}

/* USER CODE END 4 */
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


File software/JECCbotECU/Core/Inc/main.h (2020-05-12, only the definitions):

#define LIDAR_TX_Pin GPIO_PIN_2
#define LIDAR_TX_GPIO_Port GPIOA
#define LIDAR_RX_Pin GPIO_PIN_3
#define LIDAR_RX_GPIO_Port GPIOA
#define INH34_Pin GPIO_PIN_4
#define INH34_GPIO_Port GPIOA
#define INH12_Pin GPIO_PIN_5
#define INH12_GPIO_Port GPIOA
#define PWM4_Pin GPIO_PIN_6
#define PWM4_GPIO_Port GPIOA
#define PWM3_Pin GPIO_PIN_7
#define PWM3_GPIO_Port GPIOA
#define PWM2_Pin GPIO_PIN_0
#define PWM2_GPIO_Port GPIOB
#define PWM1_Pin GPIO_PIN_1
#define PWM1_GPIO_Port GPIOB
#define GPS_TX_Pin GPIO_PIN_10
#define GPS_TX_GPIO_Port GPIOB
#define GPS_RX_Pin GPIO_PIN_11
#define GPS_RX_GPIO_Port GPIOB
#define KVH_TX_Pin GPIO_PIN_9
#define KVH_TX_GPIO_Port GPIOA
#define KVH_RX_Pin GPIO_PIN_10
#define KVH_RX_GPIO_Port GPIOA
#define LIDAR_PWM_Pin GPIO_PIN_8
#define LIDAR_PWM_GPIO_Port GPIOB

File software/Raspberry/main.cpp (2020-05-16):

/*
 * main.cpp
 *
 *  Created on: May 2, 2020
 *      Author: jonas
 */
#include "JECCbotServer.h"
#include "ECU.h"
#include "DataLogger.h"

int main()
{
	JECCbotServer *server = new JECCbotServer(8000, "/home/pi/resources", 40);
    ECU *ecu = new ECU("/dev/ttyACM0", 115200);
    DataLogger *logger = new DataLogger("/home/pi/resources");

    NmeaBlob n;

	while(1)
	{
        n = ecu->getNmeaData();
        //printf("%i\n%i\n%f\n%f\n", n.heading, n.time, n.latitude, n.longitude);
        logger->logString("nmeaData.txt", "Heading: " + std::to_string(n.heading), true);
        logger->logString("nmeaData.txt", "Time: " + std::to_string(n.time), false);
        logger->logString("nmeaData.txt", "Latitude: " + std::to_string(n.latitude), false);
        logger->logString("nmeaData.txt", "Longitude: " + std::to_string(n.longitude), false);

        usleep(500000);
	}

	return 0;
}

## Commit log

2020-04-04 added kicad source
    [JECCbotECU.kicad_pcb, JECCbotECU.sch, bno055.sch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]
2020-04-04 changed directory
    [JECCbotECU.kicad_pcb, JECCbotECU.sch, bno055.sch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]
2020-04-04 added schematics pdf
2020-04-05 finished schematics
    [JECCbotECU.kicad_pcb, JECCbotECU.sch, bno055.sch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]
2020-04-05 started pcb
    [JECCbotECU.kicad_pcb, JECCbotECU.sch]
2020-04-05 component placement almost done
    [JECCbotECU.kicad_pcb, JECCbotECU.sch]
2020-04-05 pcb placement
    [JECCbotECU.kicad_pcb]
2020-04-05 finished component placement
    [JECCbotECU.kicad_pcb]
2020-04-13 finished layout
    [JECCbotECU.kicad_pcb, bno055.sch, connectors.sch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]
2020-04-14 silkscreen design
    [JECCbotECU.kicad_pcb]
2020-04-14 added silkscreen pinouts
    [JECCbotECU.kicad_pcb]
2020-04-14 improved ground
2020-04-15 updated schematics
    [JECCbotECU.kicad_pcb, JECCbotECU.sch, header.sch]
2020-04-15 moved top label
    [JECCbotECU.kicad_pcb]
2020-04-16 design rules check
    [JECCbotECU.kicad_pcb, bno055.sch, connectors.sch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]
2020-04-16 improved layout
    [JECCbotECU.kicad_pcb]
2020-04-16 checked overlay with motordriver board
2020-04-28 fixed layout and created case
    [JECCbotECU.kicad_pcb, JECCbotECU.sch, batteryadapter.stl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]
2020-04-28 added list of power pcbs
2020-04-28 added spacers
    [case.FCStd, spacer.stl, top.stl]
2020-05-11 added gcode for case
    [case.FCStd]
2020-05-16 added raspberry pi codeblocks project
2020-05-16 added case view

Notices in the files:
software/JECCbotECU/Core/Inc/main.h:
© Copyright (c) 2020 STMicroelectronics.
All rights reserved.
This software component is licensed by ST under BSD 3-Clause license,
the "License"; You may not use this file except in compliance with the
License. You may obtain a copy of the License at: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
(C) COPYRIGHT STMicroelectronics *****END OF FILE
